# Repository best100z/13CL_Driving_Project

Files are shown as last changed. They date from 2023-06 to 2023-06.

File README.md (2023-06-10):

# Project Description
The main goal of this project was to build a small scale self-driving car. This car would have several key capabilities. First, we wanted it to be able to drive to a specific set destination. Second, we needed the car to be able to avoid obstacles along the way to this destination. We expected the car to be able to perform all tasks on board. That is, as soon as it was plugged in/turned on, it would travel to its destination without any user input. To do this, we built the car, created a steering column and drive motor, and added several electronic components to perform the needed tasks. This README serves as an introduction into working with the car and as a guide to recreating the project.

So, why a self driving car? As evidenced by the popularity of Tesla, a car that can drive itself is a huge draw for consumers. Not only that, but it also has many possible applications in small scale robotics. However, we decided to focus more on the human aspect of this technology. Our car has a steering column that allows it to drive like an actual car on the road. We really wanted to see how far our car can get on a small scale without the aid of complicated devices like GPS and the other sensors Teslas use. Although our car is still a work in progress, with more testing we believe that it can overcome a large variety of obstacles it may encounter. 

For videos of the car in action, check the videos folder in this repository.

## Table of Contents
1. [Building the Car](#build)
2. [Electronic Components](#components)
3. [Real World Challenges](#challenges)
4. [Pathfinding Code](#code)
5. [Next Steps](#next)
6. [Acknowledgements](#acks)

# Building the Car
## General Car Construction
To build the platform for the car, we used a heavily modified version of the LEGO 42123 set. The key features that remained the same were the driveshaft and the steering column. Of course, this LEGO set is not required. Beyond these two key details, much of the car is open to innovation. We used the Technic pieces that came with the set to construct the frame and mounted everything on that. To mount, we used a combination of rubber bands, Duct Tape, and minimal 3D printed parts. The main uses of 3D printing were for gears and IR sensor mountings. Rubber bands were used extensively to hold the main driving stepper motor down; however, this still resulted in skipping. Therefore, once the design of the car is finalized, a solution such as strong glue or more 3D printing would be recommended.
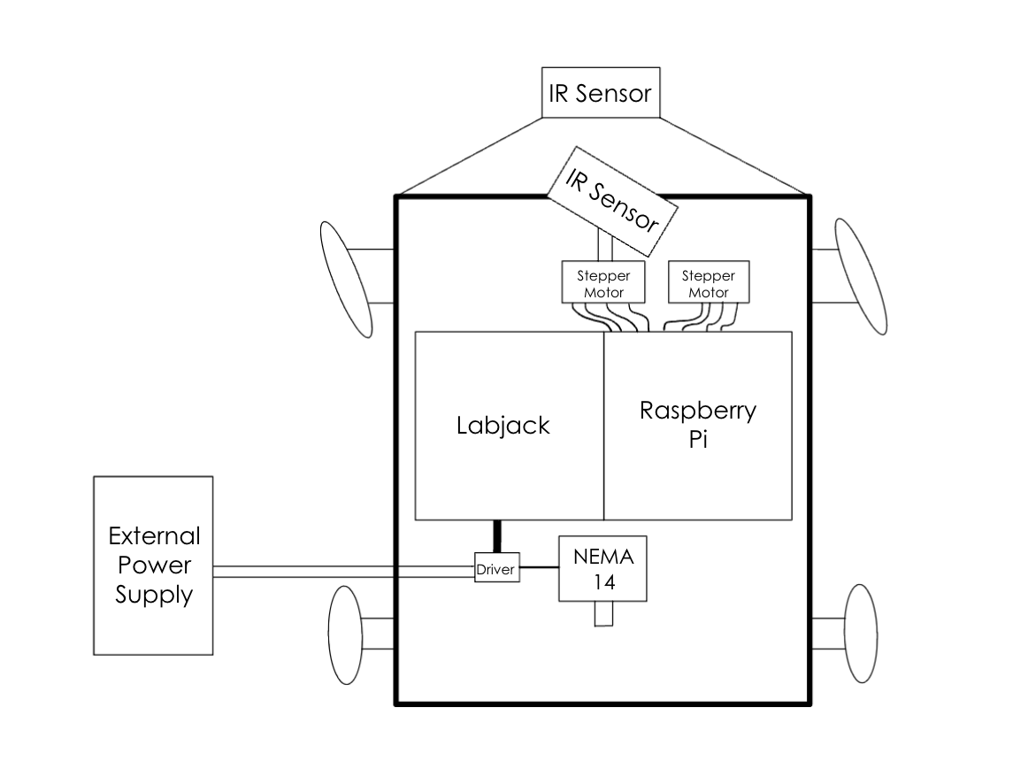
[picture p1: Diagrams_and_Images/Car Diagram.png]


Above is a diagram of the car as a whole. This diagram shows all of the main components that we will dive into further in section 3. Below are more details about the steering, driving, and IR sensing setups. 

## Steering Setup
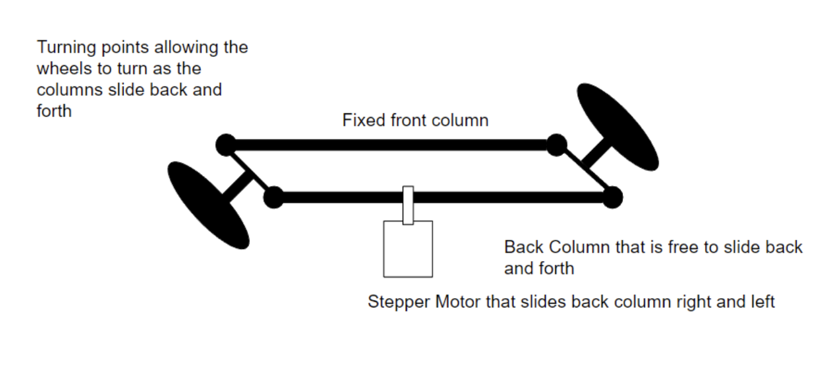
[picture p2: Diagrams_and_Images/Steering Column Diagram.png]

Our setup uses a stepper motor attached to a gear using LEGO parts. The gray piece is attached to the stepper motor through friction, and then attaches to the gear using lego pieces. This gear then controls a simple lego steering column which is from the LEGO set, but could be adjusted to fit individual needs. The 65 degree protection found in the code is dependent on this specific setup, so adjust that parameter according to individual needs.

## Driveshaft Setup
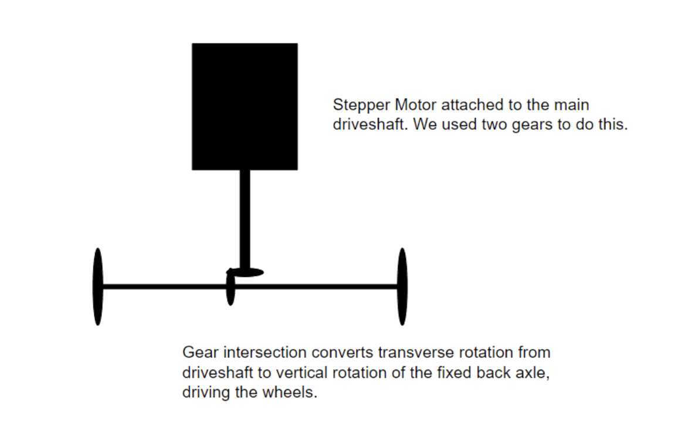
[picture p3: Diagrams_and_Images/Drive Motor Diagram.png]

We ran our NEMA 14 Motor and 3D printed gear to a LEGO gear. This then runs to a T-joint which turns the axle, allowing both wheels to drive with a fixed differential. This was the main limiter for our ability to onboard, future steps would involve mounting this motor in a permanent way with a better connection, as this setup would often experience “skipping”, where the stepper motor would turn without moving the wheels. 

## IR Sensor Setup
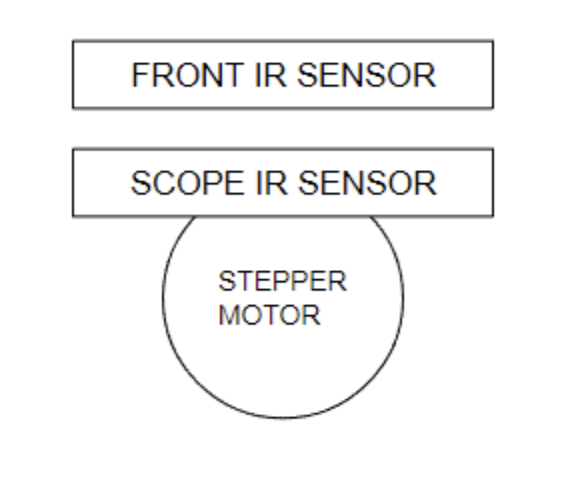
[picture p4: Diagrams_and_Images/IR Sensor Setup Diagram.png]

One sensor is fixed, facing directly forwards. As these IR sensors essentially work in two dimensions, we did not run into issues with the lower sensor detecting the ground in front and returning faulty readings. The other sensor is attached to a small stepper motor using a 3D printed piece. Our design can be found on GitHub. This is what we refer to as the “scope” in the code, and is key for scanning and decision making functionality of the car. The stepper motor is attached to the chassis of the car through another 3D printed block with a groove that perfectly fits the stepper motor. 

# Electronic Components
1. [NEMA 14 Motor and DRV8825 Driver Board](#nema)
2. [Smaller Stepper Motors](#steps)
3. [IR Sensors](#ir)
4. [Raspberry Pi](#rpi)
5. [Labjack](#labjack)

## NEMA 14 Motor and DRV8825 Driver Board
This setpper motor and driver board were chosen for a few reasons. The NEMA 14 motor has a compact size that allows it to easily fit on the car. The motor also outputs a significant amount of torque for its size, which is needed in order to onboard all of the components of the car. The driver board was chosen because it is very commonly used as an intermediary between microcontrollers such as our Raspberry Pi and the NEMA 14 motor. Lastly, this combination of driver board and motor can run on a very reasonable power supple of ~9V, which allows for the use of a 9V battery. As shown in the car diagram above, we instead used an external power supply for our tests because a battery's lifespan was a concern. Below is the pinout for the DRV8825 driver board and how we set up each pin.
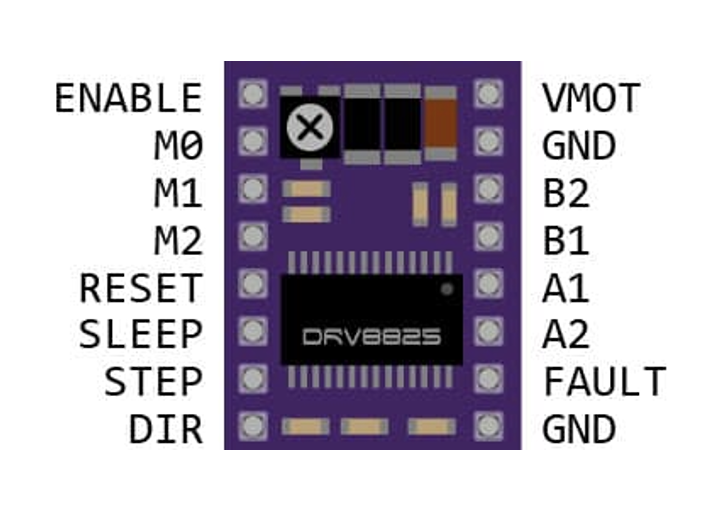
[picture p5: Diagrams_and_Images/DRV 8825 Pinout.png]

* VMOT takes DC input from 9-25 Volts. Many document that the board is susceptible to voltage spikes and run a capacitor in parallel before hooking up the VMOT and GND. We did not do that, and ran into no issues with that using a DC Power Supply. 
* GND 1 is Motor Ground, GND 2 is Logic Ground.
* B2 Is second wire of second coil – Blue for the motor we used
* B1 is first wire of second coil – Red for the motor we used
* A1 is first wire of first coil – Black for the motor we used
* A2 is second wire of first coil – Green for the motor we used (This completes NEMA wiring)
* FAULT triggers SLEEP when pulled high. Defaults to low, left unconnected with no issue
* ENABLE – pull high to disable the chip, low to enable. Left unconnected
* MO, M1, M2 – Controls step size, refer to attached image:

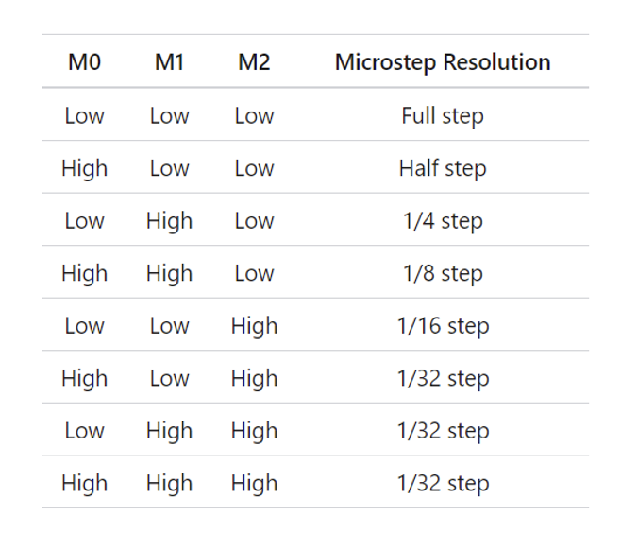
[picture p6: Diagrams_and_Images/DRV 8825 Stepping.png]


* RESET – Pull low to disable the board, High to enable. Used 5V DC.
* SLEEP – Stops power draw to the motor when pulled low. Pull high to enable power draw, and in turn enable the motor.
* STEP – Send pulse to step motor once
* DIR – Pull high for one direction, leave low for the other. 

**NOTE:** Make sure to adjust the potentiometer in order to control the max current delivered by the board. If you do not do this correctly the motor WILL NOT work. To do this, measure the voltage of the small screw on the board, using a multimeter, with the other end attached to the ground of the board. This voltage reading should be half the maximum current of your stepper motor, i.e. if your stepper motor is rated for 1 Amp, you are aiming for a voltage of about 500mV. If it isn't, adjust this screw carefully until it is.  

## Smaller Stepper Motors
For this project, we used two smaller stepper motors as discussed in section 2. These were 28BYJ-48 stepper motors, driven by ULN2003 driver boards. These specific parts were chosen due to size and ease of access. Any small stepper motor will likely work for these functionalities. However, there are some constraints. The stepper motor for the steering column needs to output enough torque to overcome the friction preventing the wheels from turning. Also, you may want to consider a stepper motor/driver board combination that can full step quickly in order to make the car operate at higher speeds. For our project, these two motors were microstepped. This was done due to constraints of the electronics, but it also came with a significant advantage: precision. Weighing precision vs. speed is a key challenge of this project. 
Another advantage of this combination of motor/driver is that it is largely plug and play. The stepper motor has a combined cable that plugs directly into the driver board's output pins, so no testing is needed to ensure correct connections. More details on the pinouts for these driver boards are shown in the Raspberry Pi section.

## IR Sensors
The infrared Sensors that we used in this project were Sharp GP2Y0A21YK sensors. These IR sensors were chosen because they provide information in the range 10-80 cm. The range that we will use in the project is around 30-50cm, so this is right in the middle of the range of this sensors. Another reason to use IR sensors instead of another sensor such as ultrasonic sensing it for its directionality. The IR sensor measures in a 10 degree triangle in front of the sensor. Because our project operates only in two dimensions, this is advantageous as the signal won't detect anything not in the plane of the car. 
Once the IR sensors had been chosen, we needed to calibrate them. This was done by measuring the voltage readout of the IR sensor at 5cm increments between 10cm and 80cm. Once this data was obtained, a regression was performed to find a voltage-distance relation. Upon performing fits for both power laws and exponentials, the exponential fit was preferred due to a smaller $\chi^2$. The relationship found was: $V=3.67e^{-0.068d}+0.46$, where V is the voltage and d is the distance. This relationship held under all testing. It worked similarly well for each different IR sensor, so calibration was consistent. Another test was then performed with 30 measurements taken at each distance, with the results shown below. 
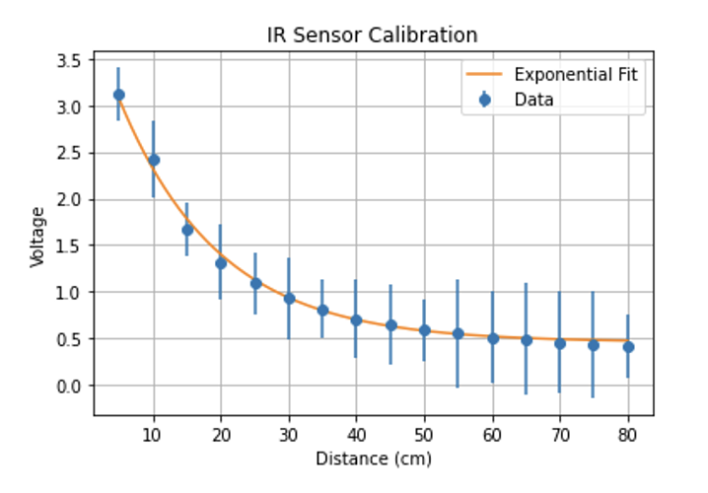
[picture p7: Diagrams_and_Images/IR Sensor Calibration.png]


The error bars on this plot are $1-\sigma$ error bars for the 30 data points at each distance. Points correspond to the mean of the data points. The error bars are also multiplied by 100 to showcase how accurate this measurement is. Becuase the calibration not only worked for each different sensor, but also entirely different sets of data, we assume that it is very accurate under these controlled conditions. It is worth noting that all of these tests were performed with a cardboard target, which was the material used for the obstacles in our final tests. This relationship is expected to vary slightly depending on the material that is being detected. 

## Raspberry Pi
The Raspberry Pi is the brains of the car in this project. It contains all of the code and will perform all of the actions required of the car once turned on. However, along with the code, there is some setup required. First of all, the Pi needs to run the code on startup. The way we do this is by changing the bash file to run the code whenever a terminal is opened, and we add a line of code that opens a terminal window whenever the Pi is turned on. The reason that we do this instead of just running the code on startup is for debugging purposes. If the UI of the Pi is connected to a monitor in some way, you can view what the Pi is doing through the opened terminal window while it runs. The Raspberry Pi will also need some Python packages that are not included in most versions of Anaconda. However, the Python environment that comes installed on Raspbian OS (which we highly recommend as the OS) contains theses packages. For any other Raspberry Pi OS, you may need different instructions. 

I will detail here the instructions on how to get the Pi to run code on startup. First, navigate to a terminal window. The native terminal program on Raspbian OS works fine. Type the following command:
```console
sudo nano ~/.config/lxsession/LXDE-pi/autostart
```
This will open a text file that you can edit. At the bottom of this file, add the line:
```console
@lxterminal
```
This will make the terminal window open on startup. Close, save, and reboot the Pi. You should see a terminal window open on startup. Once this is done, you will need to edit the .bashrc file in order to make the Pi run code on startup. Do this by running:
```console
sudo nano /home/pi/.bashrc
```
And then adding the line:
```console
sudo python /home/pi/sample.py
```
You will need to edit this line in order to fit your specific naming conventions. /home/pi/sample.py will be replaced by the path of your specific python program. For our case, it was /home/robotgrouppi/13CL_Driving_Project/Final\ Run\ Code\ Version.py. Once you've got this set up, you should see the Pi running your program in a terminal window whenever you plug it in!

The Raspberry Pi's GPIO pins will need to be used in order to provide stepping instructions to the smaller stepper motors. The code for doing this is included in "Final Run Code Version.py" in lines 16-29 and 76-89. These codes corrspond to the specific pinouts that we chose for our Raspberry Pi, shown below.

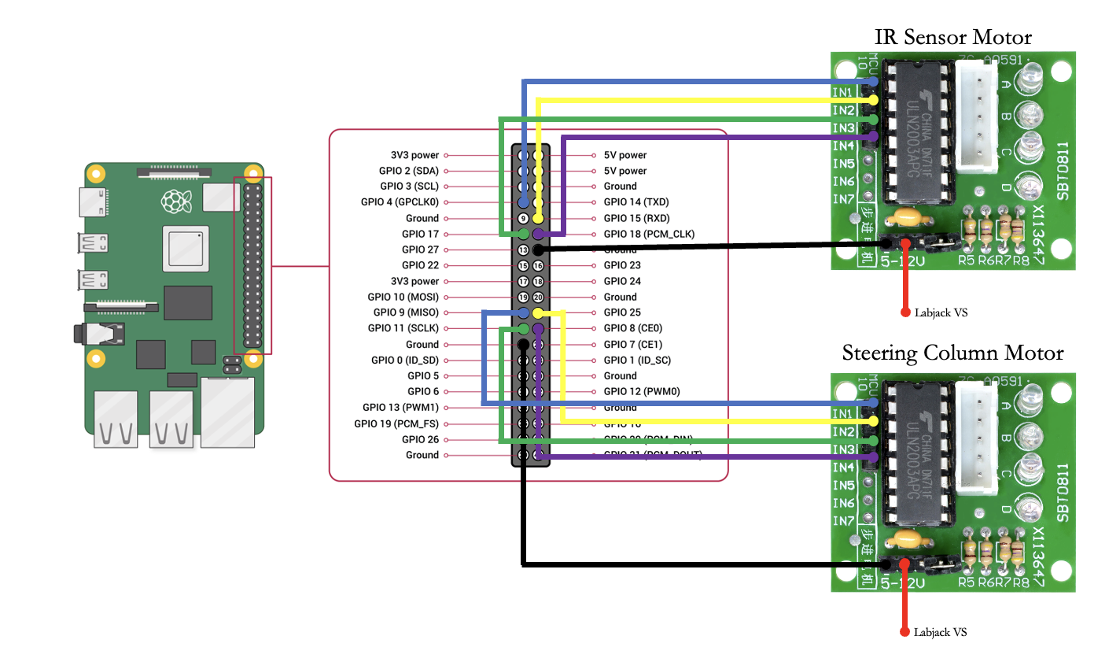
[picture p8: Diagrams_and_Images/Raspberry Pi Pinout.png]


Any of the numbered GPIO pins, despite their secondary function, can be used for the purposes needed for this project. While the Raspberry Pi is very capable of controlling the logic pins on the smaller stepper motors, we also need a Labjack for some other purposes. 

## Labjack
While this project does not require a Labjack, we used one for its analog voltage readings and as a source of 5V DC current to power the smaller stepper motors. Here is the pinout that we used and our code is designed for. However, you can do this in any way you like:
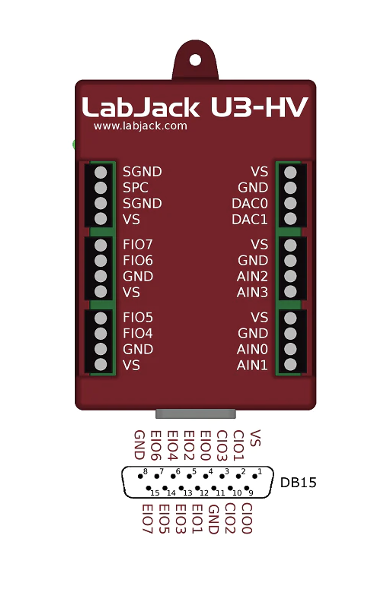
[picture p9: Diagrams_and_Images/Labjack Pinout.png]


* VS – First IR sensor power
* VS – Second IR sensor power
* VS – First stepper motor power
* VS – Second stepper motor power
* GND – IR grounds, stepper motor grounds
* AIN0 – Fixed IR sensor data cable
* AIN1 – Scope IR Sensor data cable
* FIO4 – Connected to STEP of DRV 8825 Driver Board to drive main stepper motor
* FIO5 – Connected to DIR of DRV 8825 Driver Board

# Real World Challenges
For this project, the main challenge was that it takes place in the real world. If we lived in an idealized world with perfect no slip conditions and no friction when we don't want there to be friction, everything would be easy. That is obviously not the case. We ran into several key issues when experimenting with our car that needed to be solved. These solutions ranged from coding fixes to rubber bands. as we will detail in this section.

## IR Sensors
We ran into an issue with our scanners where they would often record data incorrectly. We believe this is due to how small voltage changes lead to large distance changes in the range of 40 to 50cm.
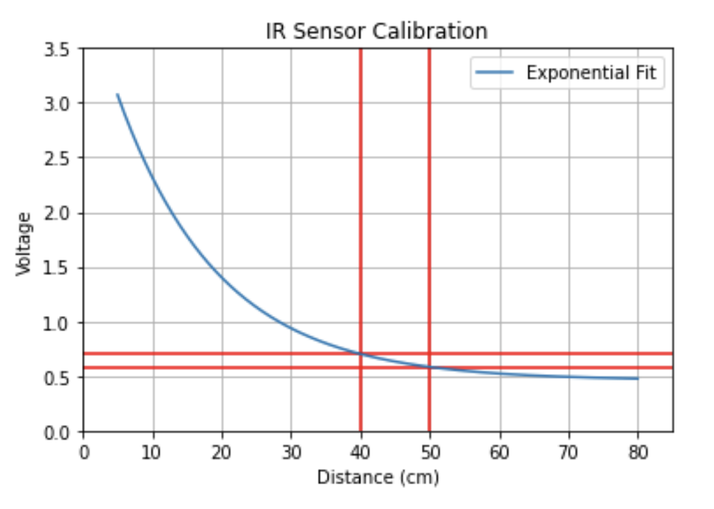
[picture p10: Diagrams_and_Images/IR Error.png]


Unfortunately, most of the time, that is the distance we are looking for obstacles in. We need about 40cm for the car to have enough space to turn. These small voltage fluctuations would lead to the car often seeing things that were not actually there. This was extremely problematic, as when the avoid loop starts the scope often won't pick anything up, leading to the car venturing off course. We solved this problem by having the car first stop and scan again. This is a more intensive scan, as it takes 30 readings. From there it finds the mode of the data. Then it takes all of the readings within 0.04cm of the mode and averages them. This is the distance that the sensor returns from this scan. This greatly improved the consistency of navigation, but highlights some of the problems with the IR sensors. 

## Motor Mounting
We consistently struggled with mounting the NEMA 14 Stepper motor, which resulted in the stepper motor often “skipping” over the LEGO piece. As all of our pathfinding is internal, this would lead to the car thinking it traveled further than it had. We used a short term solution for the duration of this project. We were able to mount the motor securely using a combination of LEGO pieces and rubber bands, as shown.
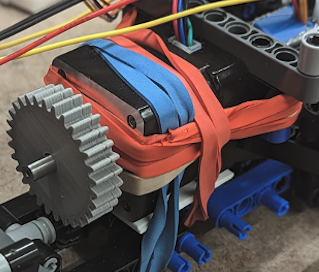
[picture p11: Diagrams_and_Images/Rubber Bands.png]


However, when we had all of the electronics onboard the motor would still skip. Our short term solution to this is just to carry the electronics alongside the car. Of course, neither of these solutions are ideal, and now that the design of the car is finalized our immediate next step would be to 3D print a better chassis and motor mount and fully onboard all of the technology. 

## Friction
One major issue we had was the friction of the car while it turned. Because there is more friction when the front wheels are turned than when they are not, the distance the car travels per step changes. This made it extremely hard to consider how the location is changing as the car is turning, as all of our location data was onboarded and dependent on a discrete correlation between steps and centimeters. Anything that adjusts this relationship, such as turning, introduced mistakes in getting to the final destination. Our solution for this was to have the car undergo a two point turn, traveling half the desired turn angle forwards, then the rest backwards. This maneuver would leave the car in the exact place it started, facing the desired angle. After doing this, it will start updating distance data using simple trigonometry to describe how the car moves relative to the destination. 

## Heading and Destination
As we were unable to create an external way to tell the car where it is, like a wireless beacon, due to time constraints, we had to handle geographic positioning through a discreet relationship between steps and centimeters. Every time we drive the car, always in 1cm steps, the car considers its heading relative to the positive x axis which is measured from the origin facing the obstacle. Positive angles always correspond to left turns. The car considers this heading as it drives to calculate where it is relative to the grid through trigonometry. This allows it to always know where it is, as well as the angle and distance to the destination. One technique we developed to reduce the chances for mistakes was to redefine the coordinate system every time the robot had a straight shot at the destination. Essentially, after every avoid loop, the car looks directly at the destination. If this path is clear, the car will turn to face it, and then update the coordinate system so that the destination is again on the positive x axis measured from the car. The car calculates the distance this point is from the original x and y values. This allows the car to dodge obstacles one at a time, reducing the chances of a breakdown in pathfinding.  

# Pathfinding Code
For our pathfinding code, we have three different loops that would allow our car to drive from a starting point to an ending point while dodging barriers along the way. Further thoughts need to be put in to find ways to dodge barriers while we are turning and also while we are driving backwards.

A general introduction to our pathfinding algorithms: we have three main loops called `sensor_loop`, `avoid_loop`, and `escape_loop`, each serving a separate role for driving our car, `sensor_loop` always drives us while we are facing towards the destination; `avoid_loop` kicks in when we are running in a path that is deviated from a straight path that runs towards the destination; `escape_loop` is our backup loop when we are running into a cave like barriers. One thing that is worth noticing is that we compute our distance to the destination using a coordinate system where we always update the direction we are facing and use the trigonometry to calculate the distance towards the final destination.

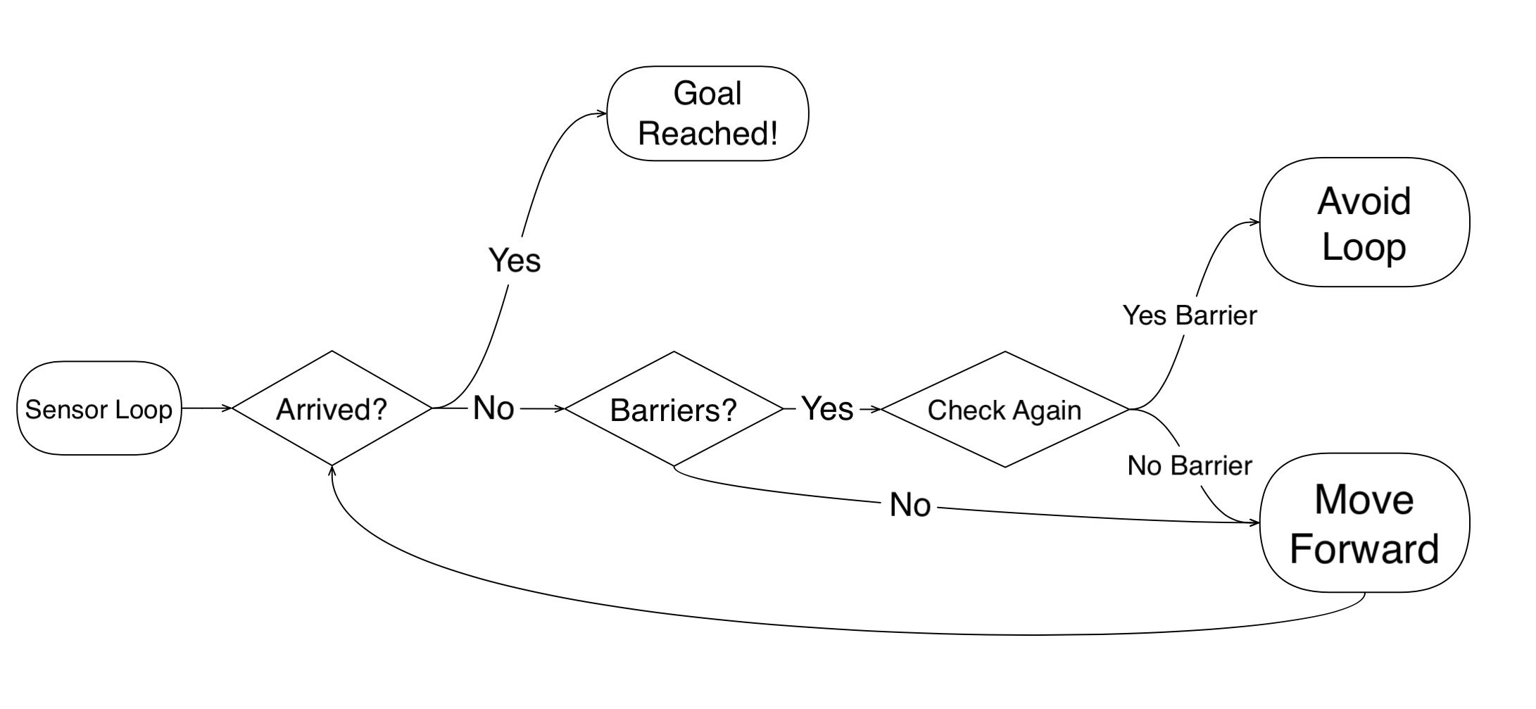
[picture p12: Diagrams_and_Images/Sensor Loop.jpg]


I will start with the main loop, which is our `sensor loop`. This is the main loop because we start our pathfinding process from here and always arrive at the destination in this loop. As mentioned before, we are only in this loop if we are facing the destination, which we can theoretically reach using only this loop if we are running in a course with no barriers. While in this loop, we are constantly driving forward with 1 cm steps (each time we step forward, we use coordinate system mentioned to record the distance the destination) and using our IR sensor(infrared sensor) to determine the distance to the nearest barriers (as mentioned in the electronics, our IR sensor works the best in the range of 10-50cm, so we ignore the barriers further than 50 cm away from us). We have tested that for a path that has no barriers in between our starting point and ending point the car can run using this loop independently. 

However, our project is to use the self-driving car to dodge obstacles, so we will possibly scan(`VoltagetoDistance()` converts the electric signals to the distance relative to our car) and find a barrier that is within 50 cm away from us. In this case we will stop our car, and since either our IR sensor or signal receiving labjack is not consistent, we made a proof check by scanning again using `IRValueMode()`(in this scanning, we used a specific method where we take 30 separate data of the voltage where each takes 0.01s, so a total of 0.3s; after that we will find the mode of those voltages, and average the voltages with some deviation from the mode). If it is our IR sensor glitching, then we will keep marching forward, otherwise we will need to deviate from the straight path towards the destination, which we will pass the information of the distance to the barrier to our `avoid_loop`.

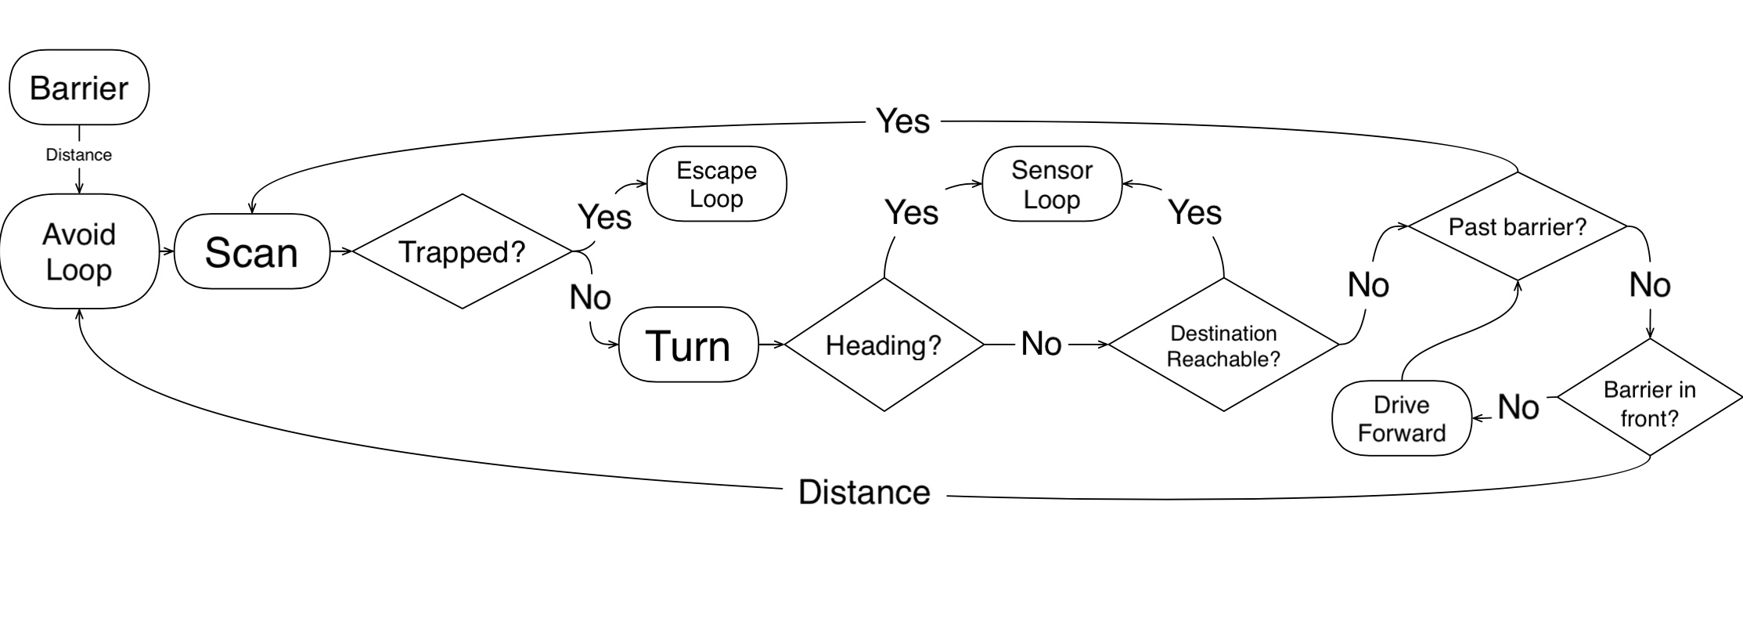
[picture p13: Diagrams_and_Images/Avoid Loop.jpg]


For our avoid loop, we are always given a distance to the barrier in front of us, so our first job is to determine how much we need to turn to avoid the obstacle. Our pathfinding algorithm here is rather naive—we are just trying to find the smallest deviation that we need to take from our straight path to the destination. We did this by our `FindMinimumAngle`, where we divide the entire front semicircle into 18 equal pieces with the same arc angle, so each will take 10 degrees (this is due to the limitation of our IR sensor that it can only tell as precise as 10 degrees), we will use the IR sensor that is connected to a stepper motor to slowly scan each section using `IRValueMode()`, which will give us a more accurate value with a lot less odds due to the inconsistency in our electronics. Since we know that our car is about 20 cm wide, which corresponds to about 15 degrees of angle on the circle of radius of 50 cm, we are looking for a 30 degree cavity which we are safe to say that our car can turn towards the middle of that cavity to dodge the barriers. Turning isn’t always easy because we are running in an obstacle course, where we need to take turning radius into consideration. So inspired by real life driving, we use `TurnInPlace` to do a three point turn (in order to turn most efficiently, we always rotate the front axle to the maximum angle possible; and then by experiment, we measured out the turning radius; and since we know that for the three point turning, we will shift the same amount of angle on the way forward and on the way back, so we take in the angle that we want to turn, divide it by half and times the radius to find the arc length, and finally, we drive the distance of the arc length intended; as a result, we turn our car facing the direction without shifting the actual position of our car too much). After that we will update our current angle that we are facing, because by trigonometry each centimeter we are moving does not represent the same displacement in x and y as before turning. Next step is to drive forward until our car is side by side along with the obstacle and while scanning to see if there are any more barriers in front at the same time. This is similar to sensor_loop, but in this case, we are only stopping if there is a barrier that is less than 20 cm away from our car because that is the enough space we need to turn our car, and we will do the same process where we will take a more accurate data for the distance of the obstacle. If we indeed have an obstacle in front, we will return the `avoid_loop` while passing the new parameter for the new barrier. This process will go on and on for as many obstacles that are in the way as the course is. Whenever we manage to actually get side by side with the obstacle we will make another 180 degree scan, where we will first find out the direction of the destination by our coordinate system, and we will then make the scan centered at the destination. We will figure out what’s the smallest deviation from a straight path towards the destination using `FindMinimumAngle`(what’s worth noticing here is that as we move deviate from the original straight path towards the destination, the path facing towards the destination will be constantly changing, but all we care about in this path finding algorithms is that we want to always find the minimum angle that deviates from the straight path to the destination at the local point).

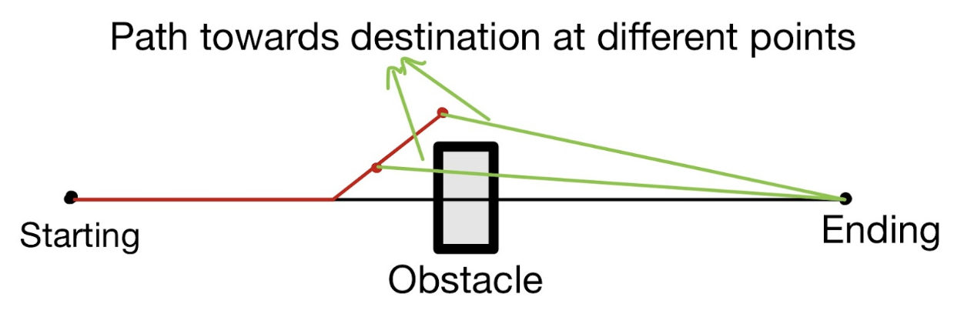
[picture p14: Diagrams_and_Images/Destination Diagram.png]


As we turned to the angle that has the smallest deviation from the center use `TurnInPlace`. Then we will need to determine if we are facing towards the destination, if the answer is yes, then we will be happily returning to the sensor loop to keep driving towards the destination while checking for potential obstacles. However, if we are unable to face the destination, we will return to the avoid loop as if there is a barrier in front that is 50cm(this is the maximum distance our IR sensor can scan with accuracy), so we will either move forward for 50cm and then check if we can turn towards the destination or if there is a new barrier we will try to dodge it using avoid loop again, through this process we will eventually turn back to the destination and return to out sensor loop.

Lastly, there is a problem that we haven’t taken into consideration, where all the previous algorithms are about dodging general barriers, however, there is a problem if we are facing a barrier that has a cave like shape, where as we are driving towards the end of the cave, we will notice that we can’t face towards any possible forward direction. So in this case the `escape_loop` (shown below) is going to help us to dodge this specific barrier. The idea is straightforward where we will drive backwards. While we are driving backwards, we are scanning towards both left and right to seek an opening for 30cm. If we do find an opening, we will then turn towards that direction and drive for 50cm, and in the end we will return the job back to our avoid loop to finally move our direction back to facing the destination. One thing worth noting is that this escape loop can only help us to dodge really shallow cave-like obstacles, for the obstacles that are deep or really large, it is not really efficient.

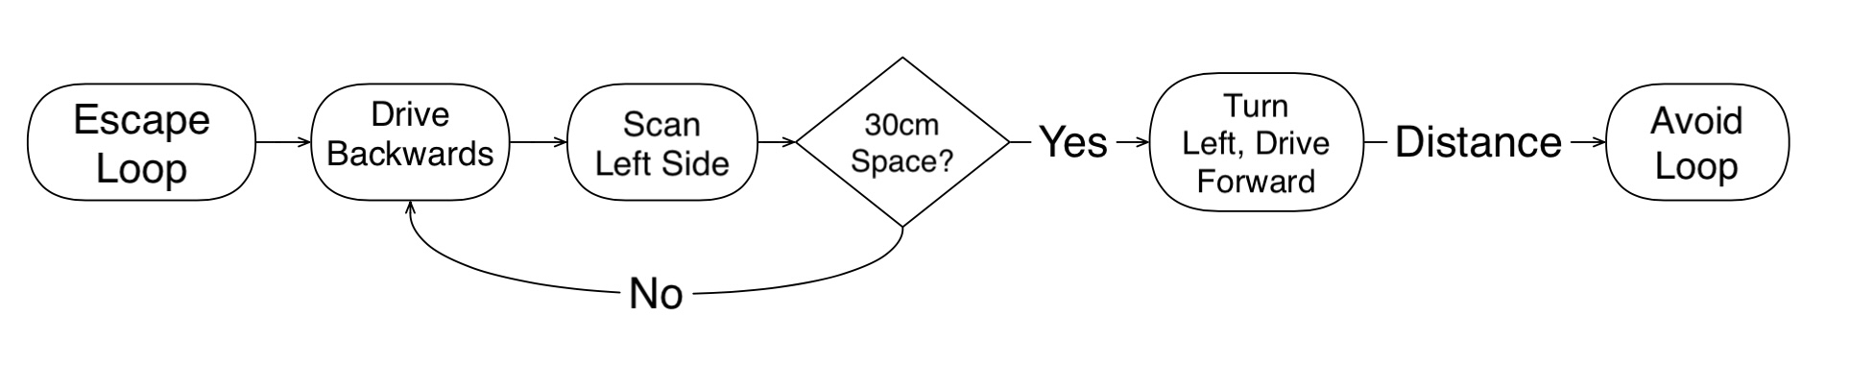
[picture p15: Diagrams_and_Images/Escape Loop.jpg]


In general, the pathfinding algorithm so far is effective for really general block shape obstacles, for more complex-shaped obstacles we may need to incorporate moving with scanning, where we constantly update the entire view of the surrounding and it will require more complex logic and more sophisticated algorithms. 

# Next Steps
While this car is completely functional, it is important to note that everything in this project is still a work in progress. There are several plans for how we would change the car given more time and resources. These updates would combat some of the challenges that we are currently seeing, and they would also allow the car's applications to expand greatly. 
## Packaging the Car
In the car's current state, it must be tethered to the Raspberry Pi, Labjack, and Power Sources. This is due to the stepper motor “skipping” when there is a lot of weight on the car, as instead of turning the driveshaft, instead the motor will move within its mounting, causing the gears to skip over each other. The motor should have plenty of torque to move the car with all of the weight on it, and therefore a solution to this would enable us to mount all of the electronics directly to the vehicle. The easiest way to address this is with a strong glue or epoxy. We opted against this as our design was often changing and we did not want to permanently mount something only to realize it needs to change. A more aesthetic solution would be 3D printing a chassis for the car, leaving space in that chassis to also mount the electronic components. This is the immediate next step in our project, as the design of our car is finalized. 
## Better Sensor Technology
While our IR sensors were effective for a small, controlled course, in any other environments they would be extremely limiting, due to their 2D scans and inconsistent behavior. With a greater budget, using LIDAR (laser imaging, detection, and ranging) instead of an IR sensor would vastly improve functionality. Relying on very similar physics, LIDAR measures the time that it takes for a laser to be sent from the device, bounce off an object, and return. Therefore, implementing it into the current system would not require many modifications to achieve the same functionality as we have now, and would unlock much greater functionality down the line. Of course, we would need to modify our scripts to handle the 3D scans LIDAR technology would allow us to take, but this is one of the first steps in making this device effective in real world situations. This technology is what most autonomous vehicles in today's market use, and its implementation would allow us to handle 3D, uncontrolled environments. 
## Improved Destination Tracking
The destination tracking within the code can be described as rusty at best. While the coding solution provides a rough estimate for where the car is trying to get, it is only as accurate as we can get our distance tracking to be. Over longer distances, the error will get larger and larger because our coding solution can never be exact. There are issues due to step sizes, and the much larger issue of skipping steps and bouncebacks of the drive motor. The inaccuracy in the turn in place command due to hardware limitations also is a source of error.

Our solution to this issue is to completely remove the coding aspect of distance tracking. The car, ideally, will not have to calculate how far it is traveling. This can be done by having some sort of signal beacon at the destination and a receiver on the car. By using multiple receivers at different positions on the car, we can triangulate the location of the beacon and know where the destination is at all times. However, on small scales, this is incredibly difficult. GPS does not have the required accuracy at this range. Radio signals are similarly long range, and a change in their signal strength is not noticable over this distance and can be attenuated significantly by obstacles. Bluetooth/Wifi signals could be a possibility with strength of signal measurements, but the Raspberry Pi is not capable of receiving signals from multiple bluetooth receivers at the same time. This could be solved with more components, such as an arduino, but there is a better solution. 

The best method for this task is using ultra-wideband transceivers, specifically DWM1001C modules from Qorvo. These have numerous advantages over other methods of distance measurement. First of all, they can use time of flight measurements instead of signal strength. This means that they have no issue with attenuation by obstacles, which we expect in our project. They also are able to be used at our ranges because of this. Hypothetically, these could be calibrated to our environment to find very accurate distance measurements, but there are physical limitations due to the speed of light and circuit speeds. They can be used, though, for triangulation, since the Pi can receive data from multiple at once. To use these UWB modules, we will need several things. We will need a J-Link debugger, which can come at a significant cost. We will also need PCB boards for the modules and microsoldering equipment to attach them. We will also need to write firmware for the devices so they can perform the tasks needed. While this would take significant time, we expect it would be the ideal way to solve many of our issues. For more information about UWB, check https://www.qorvo.com/products/p/DWM1001C and https://github.com/Decawave/dwm1001-examples.

# Acknowledgements
We would like to thank Professor Andrew Jayich, Eric Deck, and Robert Kwapisz for their help and advice with this project. We would also like to thank Raffi Shirinian, Max Kolevski, and the Instructional Lab Group at UCSB for their help with 3d printing and acquiring parts and Karsten Lansing and Tarun Kumar for allowing us to use their Raspberry Pis for this project.

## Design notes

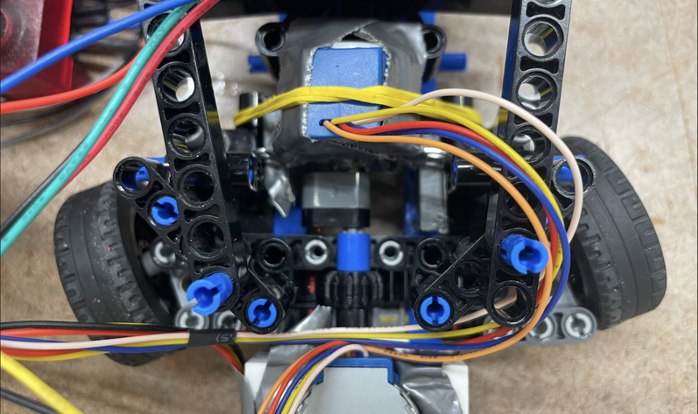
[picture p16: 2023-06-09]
Diagrams_and_Images/Steering Column Picture.png

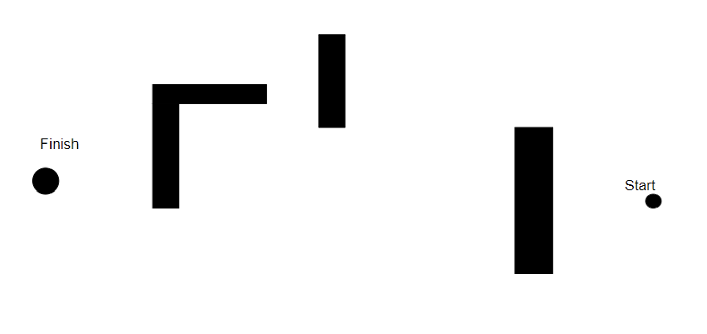
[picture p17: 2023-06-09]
Diagrams_and_Images/Example Goal Diagram.png

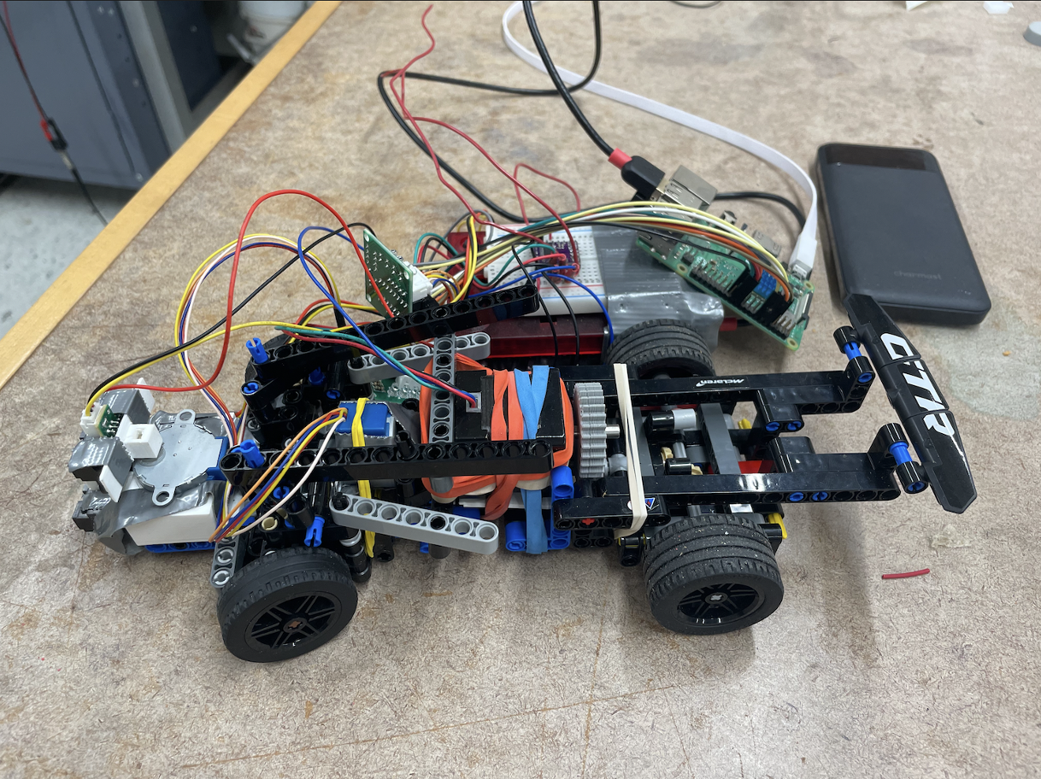
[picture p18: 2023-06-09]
Diagrams_and_Images/Whole Car Picture.png

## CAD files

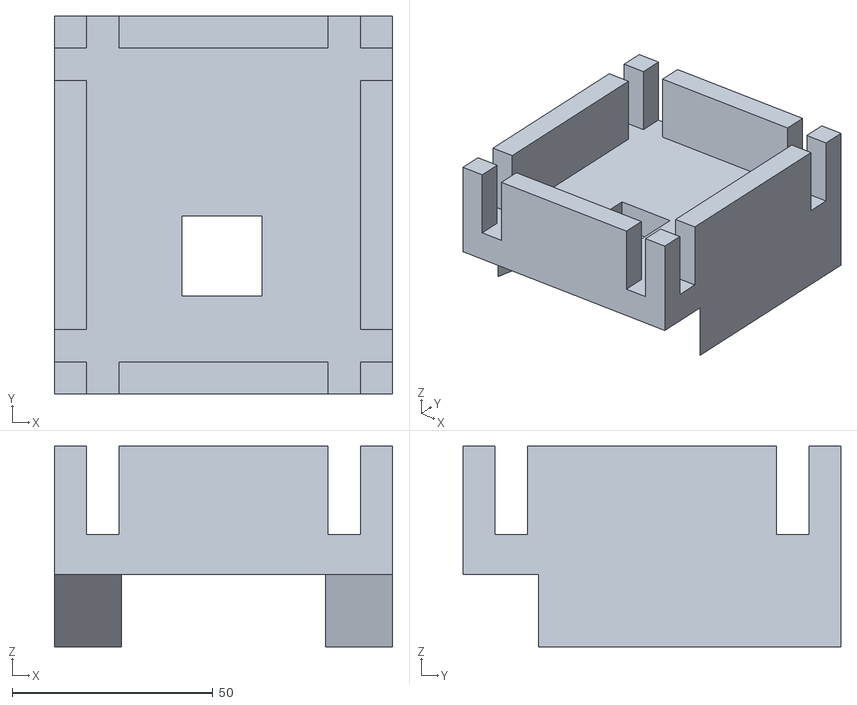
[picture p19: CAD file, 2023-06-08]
3D_Printing_Files/AllHolder.stl
84.1 x 94.0 x 50.0

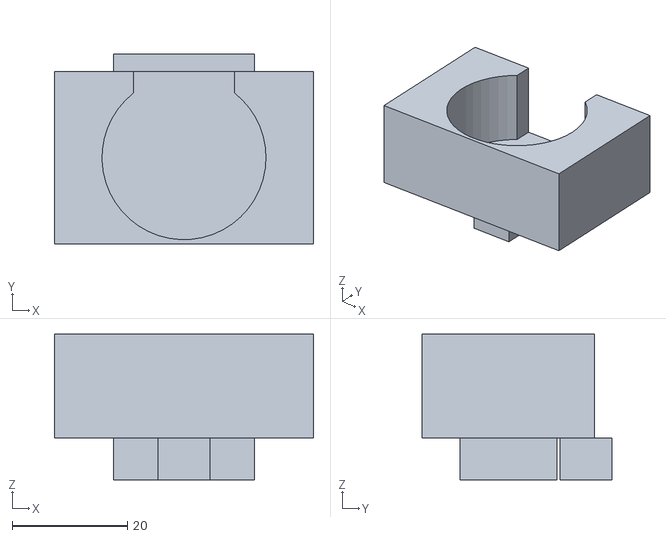
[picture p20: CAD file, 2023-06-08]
3D_Printing_Files/IRMotorHolder.stl
45.0 x 33.0 x 25.3

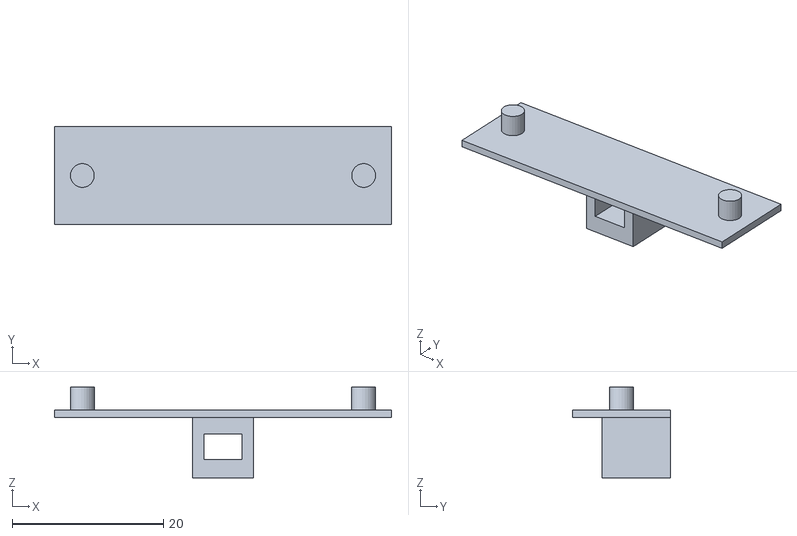
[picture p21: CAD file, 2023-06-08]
3D_Printing_Files/IRHolder.stl
44.5 x 12.9 x 12.0

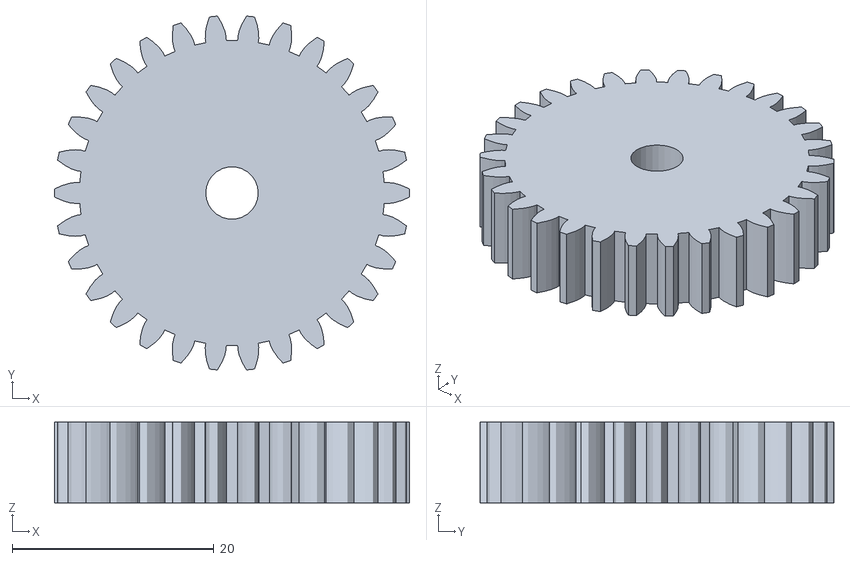
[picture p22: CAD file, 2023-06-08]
3D_Printing_Files/DriveGear.stl
35.2 x 35.1 x 8.00

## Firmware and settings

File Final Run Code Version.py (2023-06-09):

import numpy as np
import RPi.GPIO as gpio
import u3
import time
import threading
import queue



"""
@1: Define everything in a class for ease of storing state variables
"""

class piRobot():
  def __init__(self):
    #Sets the numbering scheme for the Raspberry Pi pinouts to the number scheme for just the ones labelled GPIO 0-27 - see diagrams
    #The other option is gpio.BOARD, which numbers every pin 1-40
    gpio.setmode(gpio.BCM)
    
    #This line prevents the RPi from giving a warning every time the code is run more than once without restarting
    #It can be removed with no issue
    gpio.setwarnings(False)
    
    #This loop sets every GPIO pin on the RPi to a digital in/out pin
    for i in range(28):
      gpio.setup(i, gpio.OUT)
      
    #This state variable stores whether each GPIO pin is set to Off (0) or On (1)
    self.pinStates = np.zeros(28)
    
    #This state variable stores the direction the pivoting IR sensor is facing relative to the car
    #A value of 0 is straight ahead, positive is left, and negative is right
    self.irangle = 0 
    
    #This variable stores the destination that the car is moving towards
    #This variable is updated every time the car moves
    self.destination = np.array([0,0])
    
    #This stores the direction that the car is moving in, relative to the x-axis as defined by the destination
    #Sign conventions are the same as the IR sensor
    self.heading = 0 
    
    #These lines initialize the Labjack
    self.labjack = u3.U3()
    self.labjack.configU3()    
    
    #This stores angle for the steering column, it only turns to 65 degree to either left or right; 
    #Acts as a protection and as a reminder if you forget to return the front wheel to orignial position
    self.angle = 0
    
    #This is the angle we want one slice of the 180degree ScopeScan() to be;
    self.scanslice = 10
    
    #This is the distance at which the avoid loop will trigger
    self.sensorloopTolerance = 30 
  
  #All of the below functions will just update the state variables stored in the class
  def update_angle(self, angle):
    self.angle = angle
      
  def update_irangle(self, angle):
    self.irangle = angle
    
  def update_destination(self, x, y):
    self.destination = [x,y]

  def update_heading(self, angle):
    self.heading = angle
  
  def update_fineslice(self, angle):
    self.fineslice = angle
  
  def update_sensorloopTolerance(self, dis):
    self.sensorloopTolerance = dis

  '''
    pinOnOff:
      input: array of pins
      Detail: Changes the state of every pin in the array
  '''
  
  def pinOnOff(self, numbers):
    for number in numbers:
      if self.pinStates[number]==0:
        gpio.output(number, gpio.HIGH)
        self.pinStates[number]=1
      else:
        gpio.output(number, gpio.LOW)
        self.pinStates[number]=0
  
  """
  @2: Turning Motors
  """
  
  '''
  irMotor:
    Input: (angle) to turn the ir motor and (direction) to turn
    Detail: Turn the motor in the direction for the given angle
            update the self.irangle
'''

def irMotor(self, angle = 0):
  #This is the angle of a single step on one of the stepper motors
  stepAngle = 360/4096*8
  
  #Changes the state variable to match
  self.update_irangle(self.irangle+angle)
  
  #Print is for debugging purposes
  print("ir to", self.irangle)
  
  #Finding the number of steps needed
  actualTicks = abs(angle)/stepAngle
  
  #These pinouts are detailed in the diagrams folder
  if angle >= 0:
      #The first step is different because GPIO pins 4 and 15 need to be on for the first step, but 4 is already on at the end
      #So, the second step is different. This is the same for turning right instead of left.
      #This also is the same case for the steering column motor
      self.pinOnOff([4, 15])
      time.sleep(0.01)
      self.pinOnOff([4, 17])
      time.sleep(0.01)
      self.pinOnOff([15, 18])
      time.sleep(0.01)
      self.pinOnOff([4, 17])
      time.sleep(0.01);       
      actualTicks = actualTicks - 1
      while actualTicks>0.5:
          self.pinOnOff([15, 18])
          time.sleep(0.01)
          self.pinOnOff([4, 17])
          time.sleep(0.01)
          self.pinOnOff([15, 18])
          time.sleep(0.01)
          self.pinOnOff([4, 17])
          time.sleep(0.01)      
          actualTicks = actualTicks - 1
  if angle <= 0:
      self.pinOnOff([4, 18])
      time.sleep(0.01)
      self.pinOnOff([4, 17])
      time.sleep(0.01)
      self.pinOnOff([15, 18])
      time.sleep(0.01)
      self.pinOnOff([4, 17])
      time.sleep(0.01)       
      actualTicks = actualTicks - 1
      while actualTicks>0.5:
          self.pinOnOff([15, 18])
          time.sleep(0.01)
          self.pinOnOff([4, 17])
          time.sleep(0.01)
          self.pinOnOff([15, 18])
          time.sleep(0.01)
          self.pinOnOff([4, 17])
          time.sleep(0.01)         
          actualTicks = actualTicks - 1
          
  #This block turns all pins off because remaining on could damage the motor
  for i in [4, 15, 17, 18]:
    if self.pinStates[i] == 1:
      self.pinOnOff([i])  

'''
  TurntoAngle
    input: angle: positive to the right, negative to the left, measured from centerline of the car.
    detail: make the scanning ir sensor turn to the angle
'''

def TurntoAngle(self,angle): 
    current_angle = self.irangle
    
    #Finding the turning angle needed
    final_dest = angle - current_angle
    
    #Turns the ir sensor to the angle entered
    self.irMotor(final_dest)


'''
  TurnMotor(Front Wheel)
    detail: this code is only used to turn the (front wheel) to either 65 degrees to the left or to the right
    ***has protection for the angle so it doesn't break the front motor
'''
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

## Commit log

2023-06-09 Making it pretty
    [AllHolder.stl, DriveGear.stl, IRHolder.stl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]
2023-06-09 Create Raspberry Pi Pinout.png
